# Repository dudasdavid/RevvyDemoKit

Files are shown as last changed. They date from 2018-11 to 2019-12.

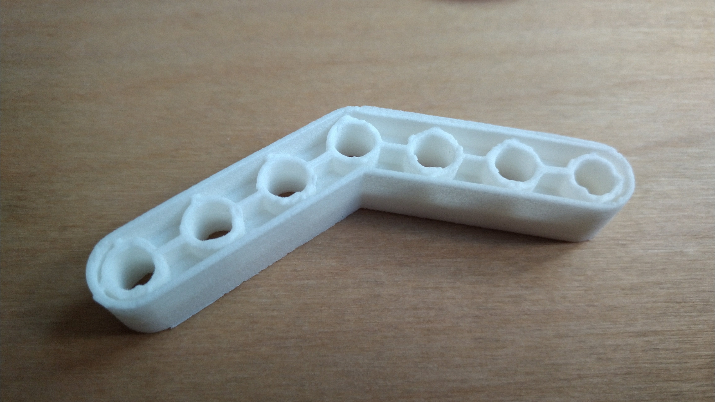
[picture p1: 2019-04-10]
Structural parts/QuotationSet2/Failure report/A135.jpg

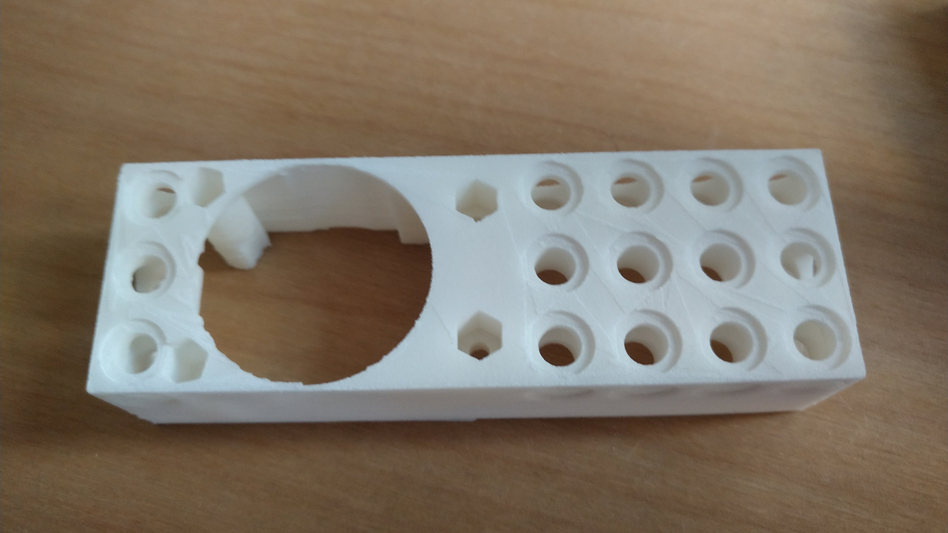
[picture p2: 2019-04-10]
Structural parts/QuotationSet2/Failure report/MOcA_1.jpg

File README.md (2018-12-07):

# RevvyDemoKit

Generated by STM32CubeMX 5.0.0 with STM32CubeF4 Firmware Package V1.22.0 / 02-November-2018

2018-11-03:
- 6x 20kHz PWM
- 6x 50Hz PWM
- WS2812 driver with DMA for 4 LEDs
- 6 ADC with DMA
- EXTI for 6 motor encoders using direction bit
- EXTI for 4 sensors
- GPIO inputs and outputs

2018-11-04:
- Cleanup of unused source files
- Cleanup of naming conventions in CubeMX project
- 4x ultrasonic distance sensors are working with 10us resolution based on TIM10
- 6x encoder signals are processed to distance [m], angle [deg] and velocity [m/s]
- Accelerometer and compass is working on I2C1 interface
- Roll and pitch angles are calculated from accelerometer
- Buzzer added TIM9_CH2

2018-11-14:
- Schematic is now uploaded
- WS2812 was unreliable with TIM+DMA, it might be a HW bug in ST's HW
- WS2812 is now driven on SPI5+DMA, pin moved to PB8 from PB7
- WS2812 library contains new functions to support SPI+DMA

2018-11-16:
- Final schematic added
- Gerber files added
- 3D model added

2018-11-17:
- Structural parts added

2018-11-19:
- WS2812 library cleanup, 3Mbit/s SPI is used, bit time is 1us

2018-11-24:
- Toolchain updated to STM32CubeMX 5.0.0 with STM32CubeF4 Firmware Package V1.22.0 / 02-November-2018
- Bluetooth tested
- Battery voltage measurement factor corrected

2018-12-07:
- Toolchain updated to STM32CubeMX 5.0.0 with STM32CubeF4 Firmware Package V1.23.0 / 23-November-2018
- First 4 WS2812 LEDs are showing the status of batteries and Bluetooth connection
- Communication protocol was updated to receive 5 bytes instead of 3
- PID controllers are added, 4 for velocity and 2 for angle

No patch is needed after code generation!

ToDo:
- Compass is not calibrated yet
- USB Host?

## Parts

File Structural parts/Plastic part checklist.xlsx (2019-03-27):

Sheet: Sum
Plastic Parts
Component / Cost Driver | RRF Part # | Color | In pool assem. | CAD file | STEP file | STL file | Volume [mm3] | Combined part | Comment | Remark/ Highlight
Straight Beams - S2x1 | S2x1 | White - P 1-1 C | OK |  |  |  | 897.51 | ok |  | According to spec; See CAD files….;
Straight Beams - S3x1 | S3x1 | White - P 1-1 C | OK |  |  |  | 1327.315 | ok
Straight Beams - S4x1 | S4x1 | White - P 1-1 C | OK |  |  |  | 1757.121 | ok
Straight Beams - S5x1 | S5x1 | White - P 1-1 C | OK |  |  |  | 2186.926 | ok
Straight Beams - S8x1 | S8x1 | White - P 1-1 C | OK |  |  |  | 3476.342 | ok
Straight Beams - S12x1 | S12x1 | White - P 1-1 C | OK |  |  |  | 5195.562 | ok
Straight Beams - S16x1 | S16x1 | White - P 1-1 C | OK |  |  |  | 6914.783 | ok
Straight Beams - S4x2 | S4x2 | White - P 1-1 C | OK |  |  |  | 3293.142 | ok
Straight Beams - S6x2 | S6x2 | White - P 1-1 C | OK |  |  |  | 4847.162 | ok
Straight Beams - S8x2 | S8x2 | White - P 1-1 C | OK |  |  |  | 6401.183 | ok
Straight Beams - S12x2 | S12x2 | White - P 1-1 C | OK |  |  |  | 9509.225 | ok
Straight Beams - S16x2 | S16x2 | White - P 1-1 C | OK |  |  |  | 12617.267 | ok
Straight Beams - S24x2 | S24x2 | White - P 1-1 C | OK |  |  |  | 18833.35 | ok
Straight Beams - S4x3 | S4x3 | White - P 1-1 C | OK |  |  |  | 4829.162 | ok
Straight Beams - S4x4 | S4x4 | White - P 1-1 C | OK |  |  |  | 6365.183 | ok
Straight Beams - S8x4 | S8x4 | White - P 1-1 C | OK |  |  |  | 12250.867 | ok
Angled Beams - A135 | A135 | White - P 1-1 C | OK |  |  |  | 3040.197 | ok
Angled Beams - A120 | A120 | White - P 1-1 C | OK |  |  |  | 3036.489 | ok
Angled Beams - A90L | A90L | White - P 1-1 C | OK |  |  |  | 2158.381 | ok
Angled Beams - A90T | A90T | White - P 1-1 C | OK |  |  |  | 2137.413 | ok
Curved Beams - CB4H | CB4H | Copper - 7579 C | OK |  |  |  | 2351.412 | ok
Curved Beams - CB6H | CB6H | Copper - 7579 C | OK |  |  |  | 3398.395 | ok
Round Beams - RB1 | RB1 | Silver - 649 C | OK |  |  |  | 829.393 | ok
Round Beams - RB2 | RB2 | Silver - 649 C | OK |  |  |  | 1271.18 | ok
Round Beams - RB3 | RB3 | Silver - 649 C | OK |  |  |  | 1712.966 | ok
Round Beams - RB4 | RB4 | Silver - 649 C | OK |  |  |  | 2154.753 | ok
Round Beams - RB8 | RB8 | Silver - 649 C | OK |  |  |  | 3921.898 | ok
Round Beams - RB12 | RB12 | Silver - 649 C | OK |  |  |  | 5689.044 | ok
Round Beams - RB16 | RB16 | Silver - 649 C | OK |  |  |  | 7456.19 | ok
Wedges - WE5x4 | WE5x4 | Gold - 7563 C | OK |  |  |  | 4241.774 | ok
Connector Triangle CT2x2 | CT2x2 | Blue - 285 C | OK |  |  |  | 2245.569 | ok
Connector Cubes - CC1x1 | CC1x1 | Blue - 285 C | OK |  |  |  | 1312.221 | ok
Connector Cubes - CC2x2 | CC2x2 | Blue - 285 C | OK |  |  |  | 3499.375 | ok
Connector Pins - CP1x1 | CP1x1 | Red - 185 C | OK |  |  |  | 387.607 | ok
Connector Pins - CP2x1 | CP2x1 | Copper - 7579 C | OK |  |  |  | 543.138 | ok
Connector Pins - CP2x2 | CP2x2 | Gold - 7563 C | OK |  |  |  | 698.668 | ok
Wheels - WHrM | WHrM | White - P 1-1 C | OK
Wheels - WHtM | WHtM | Black - Neutral Black C | OK
Gears - G20 | G20 | Blue - 285 C | OK |  |  |  | 1227.196 | ok
Gears - G40 | G40 | Blue - 285 C | OK |  |  |  | 4843.868 | ok
Gears - G60 | G60 | Blue - 285 C | OK |  |  |  | 6677.019 | ok
Elevators - EL8 | EL8 | Blue - 285 C | OK |  |  |  | 5425.347 | ok
Axels - AXp2c | AXp2c | Black - Neutral Black C | OK |  |  |  | 340.899 | ok
Axels - AXp3c | AXp3c | Black - Neutral Black C | OK |  |  |  | 480.15 | ok
Axels - AXp3s | AXp3s | Black - Neutral Black C | OK |  |  |  | 418.597 | ok
Axels - AXp6s | AXp6s | Black - Neutral Black C | OK |  |  |  | 838.155 | ok
Axels - AXp12s | AXp12s | Black - Neutral Black C | OK |  |  |  | 1677.269 | ok
Axels - AXp2p | AXp2p | Black - Neutral Black C | OK |  |  |  | 340.076 | ok
Axels - AXp4p | AXp4p | Black - Neutral Black C | OK |  |  |  | 636.353 | ok |  | My suggestion is to create
Axel Beams - AXb1 | AXb1 | Red - 185 C | OK |  |  |  | 1452.922 | ok
Axel Beams - AXb3 | AXb3 | Red - 185 C | OK |  |  |  | 2350.432 | ok
Motor Cases - MOcA_1 - No conn. Side | MOcA_1 | Red - 185 C | OK
Motor Cases - MOcA_2 - Conn. Side | MOcA_2 | Red - 185 C | OK
Motor Horns - MOhA_1 - Pin inside | MOhA_1 | Red - 185 C | OK
Motor Horns - MOhA_2 - No pin inside | MOhA_2 | Red - 185 C | OK
Brain Case - BRcA_1 Bottom | BRcA_1 | Black - Neutral Black C | OK |  |  |  |  |  |  | do we want a different finish?
Brain Case - BRcA_2 Top | BRcA_2 | Black - Neutral Black C | OK |  |  |  |  |  |  | do we want a different finish?
Brain Case - BRcA_3 Logo part | BRcA_3 | Mixed | OK |  |  |  |  |  |  | do we want a different finish?
Ultrasonic Sensor Case - UScA_1 Conn side | UScA_1 | Red - 185 C | OK
Ultrasonic Sensor Case - UScA_2 No conn side | UScA_2 | Red - 185 C | OK
Bumper Switch Case - BUcA_1 Conn side | BUcA_1 | White - P 1-1 C | OK
Bumper Switch Case - BUcA_2 No conn side | BUcA_2 | White - P 1-1 C | OK
Bumper Switch Case - BUcA_3 Button | BUcA_3 | Red - 185 C | OK
Rubber Bands - RBs | RBs | ?
Rubber Bands - RBm | RBm | ?
Caster Wheel Base - CWbA | CWbA | Blue - 285 C | OK
AA Battery Pack Case - BAcA_1 | BAcA_1 | Black - Neutral Black C | OK
AA Battery Pack Case - BAcA_2 | BAcA_2 | Black - Neutral Black C | OK
Parts not needed:
Washers - WashS | WashS | Any color |  |  |  |  |  |  | Not needed
Wedges - WE5x8 | WE5x8 | Gold - 7563 C |  |  |  |  | Not needed | xxx | Not needed
Connector Triangle CT3x3 | CT3x3 | Blue - 285 C |  |  |  |  | 3493.933 | ok | Not needed
Axels - AXp3p | AXp3p | Black - Neutral Black C |  |  |  |  | 497.102 | ok | Not needed
Straight Beams - S24x1 | S24x1 | White - P 1-1 C |  |  |  |  | 10353.225 | ok | Not needed
Angled Beams - A90P | A90P | White - P 1-1 C |  |  |  |  | 2588.186 | ok | Not needed

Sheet: Color Codes
Name | Red | Green | Blue
Black - Neutral Black C | 26 | 26 | 26
Blue - 285 C | 2 | 100 | 255
Copper - 7579 C | 198 | 83 | 35
Gold - 7563 C | 213 | 154 | 44
Red - 185 C | 230 | 3 | 18
Silver - 649 C | 236 | 236 | 236
White - P 1-1 C | 255 | 255 | 255

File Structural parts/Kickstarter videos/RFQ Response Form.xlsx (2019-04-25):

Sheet: RFQ Cost Drivers
Client: | Revolution Robotics Foundation (a 501c3 registered non-profit charity)
Product Name: | Educational Robotics Kit
Instructions: | Please complete the RFQ by entering data into each green shaded cell in this worksheet. Responses due by February 28th.
Robot Brain (1 per kit)
Component / Cost Driver | RRF Part # | Requirements | Additional Notes | CM Comments & Assumptions | Design Costs | One-Time Set-up Costs | Trial Run of 1,000 kits | 5,000 kit production run | 10,000 kit production run
RaspberryPi Zero W | PiZWA | Must be an official RaspberryPi Zero W | If CM cannot procure in sufficient volume, then Revolution Robotics will supply these to the CM.
16GB TF Card (Micro) | TF16gbA | Class 10 UHS U1 - to be selected by CM
TF Card Imaging | (not a part) | Customer will provide the software to be imaged onto the TF Card. No software to be developed by CM.
Brain LED PCB (including components) | BRled1 | See "Brain LED PCB" folder in OneDrive for specifications | Include full BoM cost here.
Brain LED Assembly | BRledA | See "Brain LED PCB" folder in OneDrive for specifications
Carrier Board Component #1 | JHY813270 | Battery, Li-Ion, 3.7V, 2000mAh, 8.1x32x70.5, 0/+45 | 1 per kit
Carrier Board Component #2 | CC0402KRX5R6BB475 | Capacitor, 4.7u, 10V, X5R, 10%, 0402 | 2 per kit |  | please provide all prices on a "per kit" basis
Carrier Board Component #3 | CL31A106KAHNNNE | Capacitor, 10u, 25V, X5R, 10%, -55/+85, 1206 | 29 per kit
Carrier Board Component #4 | CC0402KRX7R7BB104 | Capacitor, 100n, 16V, X7R, 10%, 0402 | 43 per kit
Carrier Board Component #5 | CL21A226KPCLRNC, CC0805MKX5R7BB226 | Capacitor, 22u, 10V, X5R, 10%, -55/+85, 0805, Capacitor, 22u, 16V, X5R, 20%, -55/+85, 0805 | 8 per kit
Carrier Board Component #6 | CC0402KRX7R7BB103 | Capacitor, 10n, 16V, X7R, 10%, 0402 | 12 per kit
Carrier Board Component #7 | GCM155R71H222KA37D | Capacitor, 2.2n, 50V, X7R, 10%, -55/+125, 0402 | 3 per kit
Carrier Board Component #8 | CC0402KRX5R7BB105 | Capacitor, 1u, 16V, X5R, 10%, 0402 | 9 per kit
Carrier Board Component #9 | CC0603KRX5R7BB475 | Capacitor, 4.7u, 16V, X5R, 10%, -55/+85, 0603 | 2 per kit
Carrier Board Component #10 | CC0402KRX7R9BB102 | Capacitor, 1n, 50V, X7R, 10%, 0402 | 1 per kit
Carrier Board Component #11 | C0402C224K9PACTU | Capacitor, 220nF, 6.3V, X5R, 10%, -55/+85, 0402 | 1 per kit
Carrier Board Component #12 | CC0402KRX7R7BB333 | Capacitor, 33n, 16V, X7R, 10%, 0402 | 1 per kit
Carrier Board Component #13 | GRPB051VWVN-RC | Conn, Header, Vertical, 5POS, P-1.27, -40/+105, TH | 1 per kit
Carrier Board Component #14 | RJHSE538103 | Conn, RJ-45, Right Angle, 3pos, Shielded, -55/+85, TH | 2 per kit
Carrier Board Component #15 | PJ-037A | Conn, DC Jack, 2pos, 2.1m - 5.5mm, TH | 1 per kit
Carrier Board Component #16 | PPTC202LJBN-RC | Conn, Header,RA, Female, 20x2POS, P-2.54mm, -40/+105, TH | 1 per kit
Carrier Board Component #17 | RJHSE538104 | Conn, RJ-45, Right Angle, 4pos, Shielded, -55/+85, TH | 1 per kit
Carrier Board Component #18 | BM05B-SRSS-TB(LF)(SN) | Conn, Header, Vertical, Male pin 5POS, P-1mm, -25/+85, SMD | 1 per kit
Carrier Board Component #19 | CPDQ5V0-HF | Diode, TVS, 5VWM, 18.6VC, -40/+125, SOD-923F | 24 per kit
Carrier Board Component #20 | LXES15AAA1-133 | Diode, TVS, 15V, -40/+85, 0402 | 13 per kit
Carrier Board Component #21 | PDS1040Q-13 | Diode, Schottky, AEC-Q101, 40V, 10A, -65/+150, POWERDI5 | 1 per kit
Carrier Board Component #22 | TPD6E001RSER | Diode, TVS, 6-ch, 5VWM, 11VC, -55/+150, UFQFN-10 | 3 per kit
Carrier Board Component #23 | CPDQ3V3-HF | Diode, TVS, 3.3VWM, 18.6VC, -40/+125, SOD-923F | 20 per kit
Carrier Board Component #24 | BAT54GWJ | Diode, Schottky, 30V, 200mA, -55/+150, SOD-123 | 8 per kit
Carrier Board Component #25 | BLM18AG121SN1D | Ferrite Bead, 0.5A, 120 Ohm/100MHz, -55/+125, 0603 | 2 per kit
Carrier Board Component #26 | BKP1005EM600-T | Ferrite Bead, 1.7A, 60 Ohm/100MHz, -55/+85, 0402 | 1 per kit
Carrier Board Component #27 | BKP1005EM221-T | Ferrite Bead, 1A, 220Ohm/100MHz, -55/+85, SMD, 0402 | 4 per kit
Carrier Board Component #28 | BKP1005HS221-T | Ferrite Bead, 0.8A, 220 Ohm/100MHz, -55/+85, 0402 | 4 per kit
Carrier Board Component #29 | 0ZCK0075FF2E | Fuse, PTC, Resettable, 0.75A, 6V, 0805 | 20 per kit
Carrier Board Component #30 | BRL3225T100K | Inductor, 10uH, 0.7A, 10%, 420mOhm, Wirewound, -40/+105, 3.2x2.5x1.7 | 1 per kit
Carrier Board Component #31 | IHLP2020BZER1R0M11 | Inductor, 1uH, 7A, 20%, 18.1mOhm, Shielded, -55/+125, 5.18x5.18x2 | 2 per kit
Carrier Board Component #32 | Raspberry Pi Zero W | 1Ghz CPU, 512MB RAM, Bluetooth 4.1, 802.11 b/g/n wireless LAN | 1 per kit
Carrier Board Component #33 | PRPC020DAAN-RC | Conn, Header, Male, 20x2POS, P-2.54mm, -40/+105, TH | 1 per kit
Carrier Board Component #34 | SHR-05V-S-B | Conn, Female Socket, Housing, 5 pin, 1 mm | 1 per kit
Carrier Board Component #35 | SSH-003T-P0.2-H | Crimp Receptacle Terminal, Female, 28-32AWG | 6 per kit
Carrier Board Component #36 | NX7002AK,215 | MOSFET, N-CH, 60V, 190mA, -55/+150, TO-236AB | 16 per kit
Carrier Board Component #37 | DMP3099L-13 | MOSFET, P-CH, 30V, 3.8A, -55/+150, SOT-23 | 1 per kit
Carrier Board Component #38 | SSM3J35AMFV,L3F | MOSFET, P-CH, 20V, 250mA, -55/+150, SOT-723 | 1 per kit
Carrier Board Component #39 | RC0402FR-0710KL | Resistor, 10K, 0.063W, 1%, -55/+155, 0402 | 5 per kit
Carrier Board Component #40 | RC0402FR-07100KL, [NoValue] | Resistor, 100K, 0.063W, 1%, -55/+155, 0402, Resistor, 100K, 0.0625W, 1%, 0402 | 10 per kit
Carrier Board Component #41 | RC0402FR-0747KL | Resistor, 47K, 0.063W, 1%, -55/+155, 0402 | 44 per kit
Carrier Board Component #42 | RC0402FR-07680RL | Resistor, 680, 0.0625W, 1%, 0402 | 20 per kit
Carrier Board Component #43 | RC0402FR-07100RL | Resistor, 100, 0.063W, 1%, -55/+155, 0402 | 29 per kit
Carrier Board Component #44 | RC0402FR-071KL | Resistor, 1K, 0.063W, 1%, -55/+155, 0402 | 4 per kit
Carrier Board Component #45 | RC0402FR-0730KL | Resistor, 30K, 0.0625W, 1%, 0402 | 1 per kit
Carrier Board Component #46 |  | Resistor, 2K, 0.0625W, 1%, 0402 | 1 per kit
Carrier Board Component #47 | RC0402FR-071ML | Resistor, 1M, 0.0625W, 1%, 0402 | 2 per kit
Carrier Board Component #48 | RC0402FR-07910KL | Resistor, 910K, 0.0625W, 1%, 0402 | 1 per kit
Carrier Board Component #49 | RC0402FR-07240KL | Resistor, 240K, 0.0625W, 1%, 0402 | 1 per kit
Carrier Board Component #50 | RC0402FR-07200KL | Resistor, 200K, 0.0625W, 1%, 0402 | 1 per kit
Carrier Board Component #51 | RC0402FR-07820KL | Resistor, 820K, 0.0625W, 1%, 0402 | 1 per kit
Carrier Board Component #52 | RC0402FR-07205KL | Resistor, 205kOhms, 1%, 0.063W, -55/+155, 0402 | 1 per kit
Carrier Board Component #53 | RC0402FR-0720KL | Resistor, 20K, 0.0625W, 1%, 0402 | 2 per kit
Carrier Board Component #54 | RC0402FR-07270RL | Resistor, 270, 0.0625W, 1%, 0402 | 1 per kit
Carrier Board Component #55 | RC0402FR-07150RL | Resistor, 150, 0.0625W, 1%, 0402 | 1 per kit
Carrier Board Component #56 | RC0402FR-074K7L | Resistor, 4.7K, 0.063W, 1%, -55/+155, 0402 | 16 per kit
Carrier Board Component #57 | RC0402FR-07150KL | Resistor, 150K, 0.0625W, 1%, 0402 | 4 per kit
Carrier Board Component #58 | 500SDP1S1M7QEA | Conn, Slide Switch, Vertical, DPDT, Shielded, 3.81mm, -20/+85, TH | 1 per kit
Carrier Board Component #59 | ATSAMD51P19A-AUT | IC,MCU,32-bit,ARM Cortex M4,Flash 512K,1.8-3.6V,-40/+85, TQFP-128 | 1 per kit. Must be an official Microchip MCU model ATSAMD51P19A-AU; If CM cannot procure in sufficient volume, then Revolution Robotics will supply these to the CM. | Please indicate if the MCU will be procured in Reels or in Trays
Carrier Board Component #60 | ACS711KEXLT-15AB-T | IC, Hall effect current sensor, 15.5A, 3 - 5.5V, 90mV/A, -40/+125, 12-QFN | 1 per kit |  |  |  |  |  |  | 1 per kit
Carrier Board Component #61 | LDL212PU50R | IC, VolReg, LDO, 18V/5V, 1.2A, -40/+125, DFN-6 | 6 per kit |  |  |  |  |  |  | 6 per kit
Carrier Board Component #62 | NTS0104GU12,115 | IC,4-Ch Level Translator Bidir, 2.3V - 5.5V, 20Mbps, -55/+125, 12-XQFN | 4 per kit |  |  |  |  |  |  | 4 per kit
Carrier Board Component #63 | AP7362-33SP-13 | IC, VolReg, LDO, 5.5V/3.3V, 1.5A, -40/+85, SO-8 | 1 per kit |  |  |  |  |  |  | 1 per kit
Carrier Board Component #64 | TB6612FNG,C,8,EL | IC, 2-ch Half-bridge, 2.7V - 5.5V / 2.5V - 13.5V, -20/+85, SSOP-24 | 3 per kit |  |  |  |  |  |  | 3 per kit
Carrier Board Component #65 | BQ24092DGQR | IC, Li-Po CHRG, 1A, 4.2V, 0/+125, MSOP-10 | 1 per kit |  |  |  |  |  |  | 1 per kit
Carrier Board Component #66 | MIC2876-AYMT-TR | IC, Boost Controller, 2.5V-5.5V/Adj, 3.8A, -40/+85, TDFN-8 | 2 per kit |  |  |  |  |  |  | 2 per kit
Carrier Board Component #67 | LM393DR2GH | IC, Linear Comparator, 2-ch,2V-30V, +-1V - +-18V, 0/+70, SOIC-8 | 1 per kit |  |  |  |  |  |  | 1 per kit
Carrier Board Component #68 | IS31AP4991-GRLS2-TR | IC, Audio amplifier, Mono, 2.7V - 5.5V, -40/+85, SOIC-8 | 1 per kit |  |  |  |  |  |  | 1 per kit
Brain PCB Board | BRpcb1 | "Carrier Board"
Brain PCBA Assembly | BRpcbA | Please see "Brain PCBA" folder in OneDrive for specifications | Customer to provide firmware for CM to flash onto MCU. Pricing must include SMT and Testing; The CM's chosen 4-port RJ45 jack on the front of the brain must be no wider than 63.1mm.
Brain Test Stand | (not a part) | Please recommend test tools and proceedures along with their costs.
Battery - 2000mAh LiPo | BAbrA | Maximum space available for this LiPo battery is 85mm x 39mm x 8mm | The battery should be at least 50% charged when shipped.
Brain Case (Plastic) | BRcA | See corresponding file in OneDrive | Please indicate any labelling requirements and labelling method (e.g., polycarbonate label floated into debossed rectangle)
External Serialization | (part of label) | CM must extract the unique CPU Serial Number from each RaspberryPi Zero W and include that number on the "label" on the outside of the Brain Case.
Final Assembly | BRbeta | Fasteners TBD based on CM recommendation (e.g., snap-fit, nuts, bolts, screws, glue, etcetera); Must include a final test for successful operation.
Packaging | (TBD if required) | Includes protective packaging (e.g., in a polybag placed into a polytray in E Flute box)
Motors (5 per kit)
Component / Cost Driver | RRF Part # | Requirements | Additional Notes | CM Comments & Assumptions | Design Costs | One-Time Set-up Cost | Trial Run of 1,000 kits (5,000 motors) | 5,000 kit production run (25k motors) | 10,000 kit production run (50k motors)
6v DC Motor | MOdc6VA | See "Motor Specifications" tab & OneDrive files |  |  |  |  | Please remember to price in terms of kits which include 5 motors each
Gearbox | MOgbA | See "Motor Specifications" tab & OneDrive files
Encoder | MOenA | See "Motor Specifications" tab & OneDrive files
RJ45 female | RJ45x1A | See "Motor Specifications" tab & OneDrive files | Pinout of RJ45 to be provided by Customer; no LED's required on jack
Motor PCB Design | (design only) | See "Motor Specifications" tab & OneDrive files | Connects the encoder, RJ45 and motor contacts; designed by CM
Motor PCB Assembly | MOpcbA | See "Motor Specifications" tab & OneDrive files | Physically attaching motor contacts, encoder & RJ45 jack
Motor Horns (Plastic) | MOcA | See "Motor Specifications" tab & OneDrive files | Also see "Plastic Parts BoM" tab
Motor Case (Plastic) | MOhA | See "Motor Specifications" tab & OneDrive files | Also see "Plastic Parts BoM" tab
Final Assembly | MObeta | Fasteners TBD based on CM recommendation (e.g., snap-fit, nuts, bolts, screws, glue, etcetera); Final Assembly must include a final performance test
Packaging | (TBD if required) | Includes protective packaging (e.g., in a polybag placed into a polytray in E Flute box)
Bump Switch (1 per kit)
Component / Cost Driver | RRF Part # | Requirements | Additional Notes | CM Comments & Assumptions | Design Costs | One-Time Set-up Costs | Trial Run of 1,000 kits | 5,000 kit production run | 10,000 kit production run
Bump Switch (electronic component) | BUcomA | 5,000 click reliability
Spring for Bumper | BUsprA | 3mm travel, 1N force at the end | auxillary spring...
RJ45 female | RJ45x1A |  | Pinout by customer, no LED's required
Bump Switch PCB Design | (design only) | See "Bumper Switch" in OneDrive | super simple to connect the Bump Switch electronic component to the RJ45 jack
Bump Switch PCB Assembly | BUpcbA | See "Bumper Switch" in OneDrive | Physically attaching Bump Switch electronic component and RJ45 jack to PCB
Bump Switch Case (Plastic) | BUcA | See "Bumper Switch" in OneDrive; The plastic casing must provide a mechanical stop to protect the Bump Switch electronic component (part "BUcomA") and the PCB it attaches to from receiving too much force (e.g., exceeding the switch's nominal value) | Also see "Plastic Parts BoM" tab; CM is encouraged to reduce the size of this overall case in their design
Final Assembly | BUbeta | Fasteners TBD based on CM recommendation (e.g., snap-fit, nuts, bolts, screws, glue, etcetera); Final Assembly must include a final performance test
Packaging | (TBD if required) | Includes protective packaging (e.g., heatsealed mylar bag)
Ultrasonic Range Sensor (1 per kit)
Component / Cost Driver | RRF Part # | Requirements | Additional Notes | CM Comments & Assumptions | Design Costs | One-Time Set-up Costs | Trial Run of 1,000 kits | 5,000 kit production run | 10,000 kit production run
Ultrasonic Range Sensor (TX/RX electronic component) | UScomA | HC-SR04 sensor or equivalent | A smaller sized board is preferred.
RJ45 female | RJ45x1A | Pinout to be provided by Customer; no LED's required
Ultrasonic Range Sensor PCB Design | (design only) | CM to design to simply connect sensor to the RJ45 jack
Ultrasonic Range Sensor PCB Assembly | USpcbA | Physically attaching the sensor and RJ45 jack to PCB
Ultrasonic Range Sensor Case (Plastic) | UScA | See "Ultrasonic Sensor" in OneDrive | Also see "Plastic Parts BoM" tab; CM is encouraged to reduce the size of this overall case in their design
Final Assembly | USbeta | Fasteners TBD based on CM recommendation (e.g., snap-fit, nuts, bolts, screws, glue, etcetera); Final Assembly must include a final performance test
Packaging | (TBD if required) | Includes protective packaging (e.g., heatsealed mylar bag)
AA Battery Pack (1 per kit)
Component / Cost Driver | RRF Part # | Requirements | Additional Notes | CM Comments & Assumptions | Design Costs | One-Time Set-up Costs | Trial Run of 1,000 kits | 5,000 kit production run | 10,000 kit production run
6x Rechargeable AA Batteries | BA6xAA | 6 batteries per kit. Ni-MH 1.2V min.2000mAh | Must be packaged for storage and shipping as part of the overall kit; Should be at least 50% charged when shipped
Battery Holder Tray (holds 6x AA) | BAtrayA | Holds 6x AA batteries for easy swap of individual AA batteries by the end user without necessarily having to remove the entire battery pack casing from the robot | CM to recommend battery tray with fit & locking mechanism along with
DC plug (male end with wire) | BAplugA | Must be compatable with the DC female on the Brain (5.5mm outer diameter, 2.1mm inner diameter is preferred); Wire length of ~16cm is desired.
Battery Pack Case (Plastic) | BAcA | See "Plastic Parts BoM" tab; CM is highly to modify the design for ease of use, cost & manufacturability
Final Assembly | BAbeta | Fasteners TBD based on CM recommendation (e.g., snap-fit, nuts, bolts, screws, glue, etcetera); Final testing NOT required
Packaging | (TBD if required) | CM to recommend if protective packaging is required
Caster Wheel (1 per kit)
Component / Cost Driver | RRF Part # | Requirements | Additional Notes | CM Comments & Assumptions | Design Costs | One-Time Set-up Costs | Trial Run of 1,000 kits | 5,000 kit production run | 10,000 kit production run
Caster Wheel | CWpA | See "Caster Wheel" files in OneDrive | Can be plastic, metal or some combination to provide lowest cost solution.
Caster Wheel Base (Plastic) | CWbA | See "Plastic Parts BoM" tab; CM is highly to modify the design for cost & manufacturability | Should be similar to the S4x3 or S4x4 Plastic Part
Final Assembly | CWbeta | Fasteners TBD based on CM recommendation (e.g., snap-fit, nuts, bolts, screws, glue, etcetera); Final testing NOT required, but ball must roll smoothly when 2kg of force is applied from above the overall part
Plastic Parts | For every Plastic Part (including Cases), CM is encouraged to propose design modifications to improve cost, manufacturability and / or function
Component / Cost Driver | RRF Part # | Requirements | Additional Notes | CM Comments & Assumptions | Design Costs | One-Time Set-up Costs | Trial Run of 1,000 kits | 5,000 kit production run | 10,000 kit production run
Straight Beams - S2x1 | S2x1 | Please also refer to files with matching names in OneDrive
Straight Beams - S3x1 | S3x1
Straight Beams - S4x1 | S4x1
Straight Beams - S5x1 | S5x1
Straight Beams - S8x1 | S8x1
Straight Beams - S12x1 | S12x1
Straight Beams - S16x1 | S16x1 | Must be able to balance 4kg on each end with a fulcrum under the center of the length of the beam. It can bend, but cannot break.
Straight Beams - S4x2 | S4x2
Straight Beams - S6x2 | S6x2
Straight Beams - S8x2 | S8x2
Straight Beams - S12x2 | S12x2
Straight Beams - S16x2 | S16x2
Straight Beams - S24x2 | S24x2 | Must be able to balance 4kg on each end with a fulcrum under the center of the length of the beam. It can bend, but cannot break.
Straight Beams - S4x3 | S4x3
Straight Beams - S4x4 | S4x4
Straight Beams - S8x4 | S8x4
Angled Beams - A135 | A135
Angled Beams - A120 | A120
Angled Beams - A90L | A90L
Angled Beams - A90T | A90T
Curved Beams - CB4H | CB4H
Curved Beams - CB6H | CB6H
Round Beams - RB1 | RB1
Round Beams - RB2 | RB2
Round Beams - RB3 | RB3
Round Beams - RB4 | RB4
Round Beams - RB8 | RB8
Round Beams - RB12 | RB12
Round Beams - RB16 | RB16 | Must be able to balance 4kg on each end with a fulcrum under the center of the length of the beam. It can bend, but cannot break.
Wedges - WE5x4 | WE5x4
Connector Triangle - CT2x2 | CT2x2
Connector Cubes - CC1x1 | CC1x1
Connector Cubes - CC2x2 | CC2x2
Connector Pins - CP1x1 | CP1x1 | Should snap into the 5mm holes on beams and be able to rotate freely with minimal friction. The user experience should be similar to using a Lego Technic pin # 32556 to snap into and rotate within various connection holes along various Lego Technic beams.
Connector Pins - CP2x1 | CP2x1 | Should snap into the 5mm holes on beams and be able to rotate freely with minimal friction. The user experience should be similar to using a Lego Technic pin # 32556 to snap into and rotate within various connection holes along various Lego Technic beams.
Connector Pins - CP2x2 | CP2x2 | Should snap into the 5mm holes on beams and be able to rotate freely with minimal friction. The user experience should be similar to using a Lego Technic pin # 32556 to snap into and rotate within various connection holes along various Lego Technic beams.
Wheels - WHrM | WHrM
Wheels - WHtM | WHtM
Gears - G20 | G20
Gears - G40 | G40
Gears - G60 | G60
Elevators - EL8 | EL8
Axels - AXp2c | AXp2c
Axels - AXp3c | AXp3c
Axels - AXp3s | AXp3s
Axels - AXp6s | AXp6s
Axels - AXp12s | AXp12s
Axels - AXp2p | AXp2p
Axels - AXp4p | AXp4p
Axel Beams - AXb1 | AXb1
Axel Beams - AXb3 | AXb3
Motor Cases - MOcA | MOcA | (see above in Motors section) |  | (please price above in Motors section)
Motor Horns - MOhA | MOhA | (see above in Motors section) |  | (please price above in Motors section)
Brain Case - BRcA | BRcA | (see above in Brain section) |  | (please price above in Brain section)
Ultrasonic Sensor Case - UScA | UScA | (see above in Ultrasonic Sensor section) |  | (please price above in Ultrasonic Sensor section)
Bump Switch Case - BUcA | BUcA | (see above in Bump Switch section) |  | (please price above in Bump Switch section)
AA Battery Pack Case - BAcA | BAcA | (see above in AA Battery Pack section) |  | (please price above in AA Battery Pack section)
Caster Wheel Base - CWpA | CWpA | (see above in the Caster Wheel section) |  | (please price above in Caster Wheel section)
Other Standard Parts in Kit
Component / Cost Driver | RRF Part # | Requirements | Additional Notes | CM Comments & Assumptions | Design Costs | One-Time Set-up Costs | Trial Run of 1,000 kits | 5,000 kit production run | 10,000 kit production run
USB-A to micro-USB cable | USBcabA | Black. Between 50cm to 150cm in length. | 1 per kit. Used to recharge the LiPo battery housed in the Brain. Does NOT include a 'wall wart' or 'Edison plug' - it is just a cable.
RJ45 8pin network cable - Short | RJcabSA | ~8cm long. White. Flat ribbon cable with RJ45 jacks (8pin) on both ends. | 6 per kit. |  |  |  | (price per robot kit, not per cable)
RJ45 8pin network cable - Medium | RJcabMA | ~16cm long. White. Flat ribbon cable with RJ45 jacks (8pin) on both ends. | 4 per kit. |  |  |  | (price per robot kit, not per cable)
RJ45 8pin network cable - Long | RJcabLA | ~32cm long. White. Flat ribbon cable with RJ45 jacks (8pin) on both ends. | 2 per kit. |  |  |  | (price per robot kit, not per cable)
Rubber Bands (20+ per kit) | RB5A | Black, Red or Blue in color. Approximate diameter of 5cm (+ or - 1cm). Width of at least 2mm and not more than 5mm. | At least 20 per kit. Can be up to 50 per kit if it simplifies ordering and handling. |  |  |  | (price per robot kit, not per rubber band)
Ping Pong Balls (5+ per kit) | PPbA | Colors may vary. Should be at least 2 different colors, but every ball could be a different color. | At least 5 per kit. Can be up to 10 per kit if it simplifies ordering and handling. |  |  |  | (price per robot kit, not per ping pong ball)
Challenge Cones (4 per kit) | CCpA | Colors may vary. Should be at least 2 different colors, but every cone could be a different color. Diameter of hole on top should not be less than 41mm and not more than 65mm. Similar in size and shape to: https://www.alibaba.com/product-detail/Outdoor-soccer-and-football-plastic-marker_60690963849.html | At least 4 per kit. Can be up to 10 per kit if it simplifies ordering and handling. |  |  |  | (price per robot kit, not per cone)
USB powered 6x AA battery recharger with status LED | BAchgA | Power cable must be at least 10cm long with a USB male connector at one end. | 1 per kit. Used to recharge the AA batteries from the Battery Pack which powers the motors. Does NOT include a 'wall wart' or 'Edison plug' - it has just a USB-A end to the cable.
Kit Packing & Carton
Component / Cost Driver | RRF Part # | Requirements | Additional Notes | CM Comments & Assumptions | Design Costs | One-Time Set-up Costs | Trial Run of 1,000 kits | 5,000 kit production run | 10,000 kit production run
Blister tray(s) for expensive parts | (TBD) | Should fit snuggly into the External Carton (below) with depressions for Brain, 5 motors, sensors and potentially some other expensive and / or shock sensitive parts
Rest of parts bagged & put in loosly | (TBD) | All parts should be bagged. All bagged parts not in the Blister Tray(s) can have their bags put loosely into the External Carton (below)
Quick start guide | QSpA | 60# cover stock paper. A4 size. 4 color, 1-sided printing
Part List and Playing Field Poster | PFpA | 60# cover stock paper. The size of ~8 sheets of A4 paper (~60cm wide by ~84cm tall). Black ink + 2 PMS colors on one side, over Black (on the other side)
External Carton | KITbA | Roughly 30cm x 24cm x 16cm is our targeted size, but recommendations from CM are welcome. 4 color, 1-sided printing for the External Carton (e.g., 4-color giftbox)
Shrinkwrap of External Carton | (TBD)
Master Carton | MCbA | 5 robot kits (e.g., External Cartons) per Master Carton is preferred, but not required. Please optimize to pass drop testing & for loading onto pallets.
Regulatory / Certifications | CM needs to secure any certifications ensure kit meets any labeling requirements.
Governing Body | RRF Part # | Requirements | Additional Notes | CM Comments & Assumptions | Design Costs | One-Time Set-up Costs | Trial Run of 1,000 kits | 5,000 kit production run | 10,000 kit production run
FCC | - | CM to secure necessary certification.
RoHS | - | CM to secure necessary certification.
Prop65 | - | CM to secure necessary certification.
ASTM | - | CM to secure necessary certification.
CPSIA | - | CM to secure necessary certification.
CCC Phthalates | - | CM to secure necessary certification.
CE (Europe) | - | CM to secure necessary certification.
Bluetooth communication | - | CM to secure necessary certification.
Drop/shock test | - | CM to secure necessary certification. | IEC 60068-2-6 and IEC 60068-2-27
Other compliance requirements? (e.g., IC?) | - | Identify additional compliance or certification requirements not listed above.
Cost Summary | Design Costs | One-Time Set-up Costs | Trial Run of 1,000 kits | 5,000 kit production run | 10,000 kit production run
Total Cost (FOB to Yantian or Hong Kong)
Please indicate preferred FOB port:
Please indicate desired payment terms:
Please submit a draft MSA contract: | (please attach to RFQ response)
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

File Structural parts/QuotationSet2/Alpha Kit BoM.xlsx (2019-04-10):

Overall qty | Qty per alpha kit | RRF Part # | 20190329 shipment memos | Pack 1 bad | Pack 2 bad | Pack 3 bad | szum bad | % bad | Claim | Part Type | Status | Comment | Length (mm) | Width (mm) | Height (mm) | Volume (mm^3)
32 | 4 | S2x1 | ok | 0 | 0 | 0 | 0 | 0 | 0 | Straight Beams | OK | No change | 20 | 10 | 10 | 897.51
32 | 4 | S3x1 | ok | 0 | 0 | 0 | 0 | 0 | 0 | Straight Beams | OK | No change | 30 | 10 | 10 | 1327.315
32 | 4 | S4x1 | ok | 2 | 2 | 2 | 6 | 50 | 16 | Straight Beams | OK | No change | 40 | 10 | 10 | 1757.121
32 | 4 | S5x1 | ok | 0 | 0 | 0 | 0 | 0 | 0 | Straight Beams | OK | No change | 50 | 10 | 10 | 2186.926
32 | 4 | S8x1 | ok | 0 | 0 | 1 | 1 | 8.333333333 | 2.666666667 | Straight Beams | OK | No change | 80 | 10 | 10 | 3476.342
32 | 4 | S12x1 | ok | 2 | 3 | 2 | 7 | 58.33333333 | 18.66666667 | Straight Beams | OK | No change | 120 | 10 | 10 | 5195.562
32 | 4 | S16x1 | ok | 0 | 0 | 0 | 0 | 0 | 0 | Straight Beams | OK | No change | 160 | 10 | 10 | 6914.783
32 | 4 | S4x2 | ok | 3 | 0 | 0 | 3 | 25 | 8 | Straight Beams | OK | No change | 40 | 20 | 10 | 3293.142
32 | 4 | S6x2 | ok | 0 | 0 | 0 | 0 | 0 | 0 | Straight Beams | OK | No change | 60 | 20 | 10 | 4847.162
32 | 4 | S8x2 | ok | 0 | 0 | 0 | 0 | 0 | 0 | Straight Beams | OK | No change | 80 | 20 | 10 | 6401.183
32 | 4 | S12x2 | ok | 0 | 0 | 0 | 0 | 0 | 0 | Straight Beams | OK | No change | 120 | 20 | 10 | 9509.225
32 | 4 | S16x2 | ok | 0 | 0 | 0 | 0 | 0 | 0 | Straight Beams | OK | No change | 160 | 20 | 10 | 12617.267
32 | 4 | S24x2 | ok | 0 | 0 | 2 | 2 | 16.66666667 | 5.333333333 | Straight Beams | OK | No change | 240 | 20 | 10 | 18833.35
32 | 4 | S4x3 | ok | 0 | 0 | 1 | 1 | 8.333333333 | 2.666666667 | Straight Beams | OK | No change | 40 | 30 | 10 | 4829.162
48 | 6 | S4x4 | ok | 6 | 2 | 3 | 11 | 61.11111111 | 29.33333333 | Straight Beams | OK | No change | 40 | 40 | 10 | 6365.183
32 | 4 | S8x4 | ok | 1 | 3 | 0 | 4 | 33.33333333 | 10.66666667 | Straight Beams | OK | No change | 80 | 40 | 10 | 12250.867
32 | 4 | A135 | ok | 4 | 4 | 4 | 12 | 100 | 32 | Angled Beams | OK | No change | 40 | 40 | 10 | 3040.197
32 | 4 | A120 | ok | 0 | 0 | 0 | 0 | 0 | 0 | Angled Beams | OK | No change | 40 | 40 | 10 | 3036.489
96 | 12 | A90L | ok | 9 | 4 | 6 | 19 | 52.77777778 | 50.66666667 | Angled Beams | OK | No change | 30 | 30 | 10 | 2158.381
64 | 8 | A90T | ok | 8 | 8 | 8 | 24 | 100 | 64 | Angled Beams | OK | No change | 30 | 30 | 10 | 2137.413
32 | 4 | CB4H | ok | 3 | 3 | 3 | 9 | 75 | 24 | Curved Beams | OK | No change | 40+ | 10 | 10 | 2351.412
32 | 4 | CB6H | ok | 0 | 0 | 0 | 0 | 0 | 0 | Curved Beams | OK | No change | 60+ | 10 | 10 | 3398.395
32 | 4 | RB1 | ok | 0 | 0 | 0 | 0 | 0 | 0 | Round Beams | OK | pin, lightening thickening | 10+ | 5 | 5 | 829.393
32 | 4 | RB2 | ok | 0 | 0 | 0 | 0 | 0 | 0 | Round Beams | OK | pin, lightening thickening | 20+ | 5 | 5 | 1271.18
32 | 4 | RB3 | ok | 0 | 0 | 0 | 0 | 0 | 0 | Round Beams | OK | pin, lightening thickening | 30+ | 5 | 5 | 1712.966
32 | 4 | RB4 | ok | 0 | 0 | 0 | 0 | 0 | 0 | Round Beams | OK | pin, lightening thickening | 40+ | 5 | 5 | 2154.753
32 | 4 | RB8 | ok | 0 | 0 | 0 | 0 | 0 | 0 | Round Beams | OK | pin, lightening thickening | 80+ | 5 | 5 | 3921.898
32 | 4 | RB12 | ok | 0 | 0 | 0 | 0 | 0 | 0 | Round Beams | OK | pin, lightening thickening | 120+ | 5 | 5 | 5689.044
32 | 4 | RB16 | ok | 0 | 0 | 0 | 0 | 0 | 0 | Round Beams | OK | pin, lightening thickening | 160+ | 5 | 5 | 7456.19
32 | 4 | WE5x4 | ok | 0 | 0 | 0 | 0 | 0 | 0 | Wedges | OK | No change | 50 | 40 | 10 | 4241.774
96 | 12 | CT2x2 | ok | 1 | 1 | 4 | 6 | 16.66666667 | 16 | Connector Triangle | OK | pin change | 20+ | 20+ | 10 | 2245.569
32 | 4 | CC1x1 | ok | 2 | 4 | 4 | 10 | 83.33333333 | 26.66666667 | Connector Cubes | OK | pin change | 10+ | 10+ | 10 | 1312.221
128 | 16 | CC2x2 | ok | 7 | 11 | 9 | 27 | 56.25 | 72 | Connector Cubes | OK | pin change | 20+ | 20+ | 10 | 3499.375
600 | 75 | CP1x1 | ok | 0 | 0 | 0 | 0 | 0 | 0 | Connector Pins | OK | pin change | 20 | 5 | 5 | 387.607
200 | 25 | CP2x1 | ok | 0 | 0 | 0 | 0 | 0 | 0 | Connector Pins | OK | pin change | 30 | 5 | 5 | 543.138
80 | 10 | CP2x2 | ok | 0 | 0 | 0 | 0 | 0 | 0 | Connector Pins | OK | pin change | 40 | 5 | 5 | 698.668
32 | 4 | WHrM | ok | 0 | 0 | 0 | 0 | 0 | 0 | Wheels | OK | No change | 40 | 40 | 18
32 | 4 | G20 | ok | 0 | 0 | 0 | 0 | 0 | 0 | Gears | OK | No change | 20+ | 20+ | 8 | 1227.196
32 | 4 | G40 | ok | 3 | 4 | 3 | 10 | 83.33333333 | 26.66666667 | Gears | OK | No change | 40+ | 40+ | 8 | 4843.868
32 | 4 | G60 | ok | 2 | 4 | 4 | 10 | 83.33333333 | 26.66666667 | Gears | OK | No change | 60+ | 60+ | 8 | 6677.019
32 | 4 | EL8 | ok | 0 | 0 | 0 | 0 | 0 | 0 | Elevators | OK | No change | 80 | 10+ | 10 | 5425.347
32 | 4 | AXp2c | ok | 0 | 0 | 0 | 0 | 0 | 0 | Axels | OK | No change | 20 | 3.75 | 3.75 | 340.899
32 | 4 | AXp3c | ok | 0 | 0 | 0 | 0 | 0 | 0 | Axels | OK | No change | 30 | 3.75 | 3.75 | 480.15
32 | 4 | AXp3s | ok | 0 | 0 | 0 | 0 | 0 | 0 | Axels | OK | No change | 30 | 3.75 | 3.75 | 418.597
32 | 4 | AXp6s | ok | 0 | 0 | 0 | 0 | 0 | 0 | Axels | OK | No change | 60 | 3.75 | 3.75 | 838.155
32 | 4 | AXp12s | ok | 0 | 0 | 0 | 0 | 0 | 0 | Axels | OK | No change | 120 | 3.75 | 3.75 | 1677.269
32 | 4 | AXp2p | FAIL!!! |  |  |  | 0 | 0 | 0 | Axels | OK | pin change | 20 | 5 | 5 | 340.076
32 | 4 | AXp4p | ok | 0 | 0 | 0 | 0 | 0 | 0 | Axels | OK | pin change | 40 | 5 | 5 | 636.353
32 | 4 | AXb1 | ok | 0 | 0 | 0 | 0 | 0 | 0 | Axel Beams | OK | No change | 30 | 10 | 10 | 1452.922
32 | 4 | AXb3 | ok | 0 | 0 | 0 | 0 | 0 | 0 | Axel Beams | OK | No change | 30 | 30 | 10 | 2350.432
40 | 5 | MOcA_1 | ok | 5 | 5 | 5 | 15 | 100 | 40 | Motor Cases | OK | No change
40 | 5 | MOcA_2 | ok | 5 | 5 | 5 | 15 | 100 | 40 | Motor Cases | OK | No change
40 | 5 | MOhA_1 | ok | 0 | 0 | 2 | 2 | 13.33333333 | 5.333333333 | Motor Horns | OK | No change
40 | 5 | MOhA_2 | ok | 0 | 0 | 0 | 0 | 0 | 0 | Motor Horns | OK | No change
8 | 1 | BRcA_1 | ok | 0 | 0 | 0 | 0 | 0 | 0 | Brain Case | OK | many changes
8 | 1 | BRcA_2 | ok | 0 | 0 | 0 | 0 | 0 | 0 | Brain Case | OK | many changes
8 | 1 | BRcA_3 | ok | 0 | 0 | 0 | 0 | 0 | 0 | Brain Case | OK | many changes
8 | 1 | UScA_1 | ok | 0 | 0 | 0 | 0 | 0 | 0 | Ultrasonic Sensor Case | OK | add pin - low priority
8 | 1 | UScA_2 | ok | 0 | 0 | 0 | 0 | 0 | 0 | Ultrasonic Sensor Case | OK | add pin - low priority
8 | 1 | BAcA_1 | ok | 0 | 0 | 0 | 0 | 0 | 0 | AA Battery Pack Case | OK | change - copy new version as a whole part
8 | 1 | BAcA_2 | ok | 0 | 0 | 0 | 0 | 0 | 0 | AA Battery Pack Case | OK | change lower hood pin - low priority
8 | 1 | BUcA_1 | ok | 0 | 0 | 0 | 0 | 0 | 0 | Bumper 1 | OK | copy new version
8 | 1 | BUcA_2 | ok | 0 | 0 | 0 | 0 | 0 | 0 | Bumper 2 | OK | copy new version
8 | 1 | BUcA_3 | ok | 0 | 0 | 0 | 0 | 0 | 0 | Bumper 3 | OK | copy new version
 |  |  | 24.8

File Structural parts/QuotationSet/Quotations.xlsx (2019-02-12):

Company | Price (1 kit) USD | Price (1 kit) EUR | Price (1 kit) HUF | Price (100 kit) USD | Price (100 kit) EUR | Price (100 kit) HUF | Price (1 kit of 100) USD | Price (1 kit of 100) EUR | Price (1 kit of 100) HUF | Comment
The 3D Printer Experience | 205 | 180.4 | 57400 | 18011 | 15849.68 | 5043080 | 180.11 | 158.4968 | 50430.8 | https://app.fabnami.net/the3dprinterexperience/view_quote.html?workflow_id=Go9tR1Z5Vt
Varinex | 518.4 | 446.4 | 144000 | 15840 | 13640 | 4400000 | 158.4 | 136.4 | 44000
Silplast | 396 | 341 | 110000 | 20520 | 17670 | 5700000 | 205.2 | 176.7 | 57000
X-Plast | 712.5 | 625 | 198806.25 | 19950 | 17500 | 5566575 | 199.5 | 175 | 55665.75
Kvint-R |  |  |  |  |  |  | 0 | 0 | 0 | https://www.3dsystems.hu/en/contact.html
Materialise | 406.98 | 357 | 113558.13 | 13950.18 | 12237 | 3892467.33 | 139.5018 | 122.37 | 38924.6733 | https://onsite.materialise.com/en/Ordering/Quotation/440298
3D Hubs |  |  |  |  |  |  | 0 | 0 | 0 | https://www.3dhubs.com/3dprint
sculpteo | 325 | 286 | 91000 | 19327 | 17007.76 | 5411560 | 193.27 | 170.0776 | 54115.6 | https://www.sculpteo.com/en/print/2x4/tqx6LdiJ?uuid=VaIAJTch5fbtu5JEqlFjN
3D Systems | 402.42 | 353 | 112285.77 | 24795 | 21750 | 6918457.5 | 247.95 | 217.5 | 69184.575
Weerg |  |  |  |  |  |  |  |  |  | https://www.weerg.com/en/order
All3dp.com | 130 | 114.4 | 36400 | 11800 | 10384 | 3304000 | 118 | 103.84 | 33040
Greg |  |  |  | 26100 | 22968 | 7308000 | 261 | 229.68 | 73080
USD to EUR | 0.88
EUR to USD | 1.14
USD to HUF | 280
HUF to USD | 0.0036
EUR to HUF | 318.09
HUF to EUR | 0.0031

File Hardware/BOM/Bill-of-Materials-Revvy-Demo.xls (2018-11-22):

Comment | Description | Designator | LibRef | OC_Farnell | Quantity
ABT-414-RC | ABT-414-RC | Buzzer900 | Buzzer | 2098836 | 1
Capacitor 100 uF 25 V | Capacitor | C400, C401, C402, C403, C404, C405, C500, C502 | Capacitor 100 uF 25 V | 9451838 | 8
Capacitor 100 nF 0603 | Capacitor | C406, C407, C408, C409, C410, C411, C501, C600, C601, C602, C603, C700, C822, C823 | Capacitor 100 nF 0603 | 2896702 | 14
Capacitor 10 nF 0603 | Capacitor | C800, C801, C802, C803, C804, C805, C806, C807, C808, C809, C810, C811, C812, C813, C814, C815, C816, C817, C818, C819, C820, C821 | Capacitor 10 nF 0603 | 2896421 | 22
BZT52-B10X | Zener Diode | D500 | Diode_Zener_10V | 2851248 | 1
SSB44-E3/52T | Schottky Rectifier | D501 | Schottky_Diode_DO214AA | 1336557 | 1
BAT54S | Diode Schottky 30V 0.2A 3-Pin SOT-23 T/R | D800, D801, D802, D803, D804, D805, D806, D807, D808, D809, D810, D811, D812, D813, D814, D815, D816, D817, D818, D819, D820, D821, D822, D823, D824, D825, D826, D827, D828, D829, D830, D831, D832, D833 | BAT54S | 9526510 | 34
0ZCJ0200FF2C | Resistor | F500 | PolyFuse2A | 2834895 | 1
0ZCJ0050FF2G | Resistor | F501 | PolyFuse500mA | 2834889 | 1
6339160-1 | MJ,RJ45,SMT,SHLD,PANEL GRD | J200, J201, J202, J203, J204, J205 | 6339160-1 | 2059758 | 6
1-338088-3 | 8/8 INV.MOD.JACK | J206, J207, J208, J209 | 1-338088-3 | 1522228 | 4
STM32F4DISCOVERY | STM32F4DISCOVERY | J300 | STM32F4DISCOVERY_New | 2456732 | 1
WS2812B | Intelligent Control Led Integrated Light Source Pack Of 10 | LED600, LED601, LED602, LED603 | WS2812B |  | 4
FDS6681Z | P-channel MOSFET | Q500 | P FET FDS6681Z | 1611454 | 1
Value | N Chanel mosfet | Q900 | 2N7002 | 9845313 | 1
Resistor_10k | Resistor | R500, R900 | Resistor_10k | 2059627 | 2
Resistor_2K2 | Resistor | R600 | Resistor_2K2 | 2908362 | 1
Resistor_4k7 | Resistor | R800, R808 | Resistor_4k7 | 2059619 | 2
Resistor_1k | Resistor | R801, R802, R804, R805, R806, R807, R810, R811, R812, R814, R815, R816, R817, R818, R819, R820, R822, R823, R824, R825, R827, R828, R829, R830, R831, R832, R834, R835, R836, R837 | Resistor_1k | 2059601 | 30
Resistor_100 | Resistor | R803, R809, R901 | Resistor_100 | 2303059 | 3
Resistor_3K | Resistor | R813, R821, R826, R833 | Resistor_3K | 2073461 | 4
Resistor_18K | Resistor | R838, R840 | Resistor_18K | 2447269 | 2
Resistor_2K | Resistor | R839, R841 | Resistor_2K | 2447319 | 2
L202011MS02Q | DPDT Switch | SW500 | Switch_L202011MS02Q | 2320074 | 1
Value | IC - VNH7070 | U400, U401, U402, U403, U404, U405 | IC - VNH7070 | 2797973 | 6
LM3940IMP-3.3 | 1A Low Dropout Regulator for 5V to 3.3V Conversion 4-SOT-223 -40 to 125 | U500 | LM3940IMP-3.3 | 1469104 | 1
HC-05 | HC-05 | U700 | HC-05_Stand |  | 1
LPCR035CTP | Lightpipe |  |  | 2832150 | 4

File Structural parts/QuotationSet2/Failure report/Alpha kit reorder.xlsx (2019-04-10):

RRF Part # | Qty | Part Type
S4x1 | 18 | Straight Beams
S8x1 | 4 | Straight Beams
S12x1 | 21 | Straight Beams
S4x2 | 10 | Straight Beams
S24x2 | 7 | Straight Beams
S4x3 | 4 | Straight Beams
S4x4 | 32 | Straight Beams
S8x4 | 13 | Straight Beams
A135 | 32 | Angled Beams
A90L | 54 | Angled Beams
A90T | 64 | Angled Beams
CB4H | 24 | Curved Beams
CT2x2 | 16 | Connector Triangle
CC1x1 | 32 | Connector Cubes
CC2x2 | 78 | Connector Cubes
G40 | 32 | Gears
G60 | 32 | Gears
AXp2p | Ordered in a previous e-mail | Axels
MOcA_1 | 40 | Motor Cases
MOcA_2 | 40 | Motor Cases
MOhA_1 | 7 | Motor Horns

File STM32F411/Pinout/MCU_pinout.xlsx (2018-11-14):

Position | Name | Type | Signal | Label | Comment
92 | PB6 | I/O | I2C1_SCL | Audio_SCL [CS43L22_SCL]
25 | PA2 | I/O | ADC1_IN2 | BAT1 [ADC_IN2]
26 | PA3 | I/O | ADC1_IN3 | BAT2 [ADC_IN3]
5 | PE6 | I/O | TIM9_CH2 | BUZZER_PWM [TIM9_CH2]
64 | PC7 | I/O | USART6_RX | HM-10 [USART6 RX] | Bluetooth
63 | PC6 | I/O | USART6_TX | HM-10 [USART6 TX] | Bluetooth
61 | PD14 | Output | GPIO_Output | LD5 [Red Led]
62 | PD15 | Output | GPIO_Output | LD6 [Blue Led]
51 | PB12 | Input | GPIO_Input | LEFT1_ENC_B
81 | PD0 | I/O | GPIO_EXTI0 | LEFT1_EXTI0 | ENC_A
54 | PB15 | Output | GPIO_Output | LEFT1_FW
40 | PE9 | I/O | TIM1_CH1 | LEFT1_PWM [TIM1_CH1]
58 | PD11 | Output | GPIO_Output | LEFT1_RW
52 | PB13 | Input | GPIO_Input | LEFT2_ENC_B
82 | PD1 | I/O | GPIO_EXTI1 | LEFT2_EXTI1 | ENC_A
7 | PC13-ANTI_TAMP | Output | GPIO_Output | LEFT2_FW
42 | PE11 | I/O | TIM1_CH2 | LEFT2_PWM [TIM1_CH2]
8 | PC14-OSC32_IN | Output | GPIO_Output | LEFT2_RW
53 | PB14 | Input | GPIO_Input | LEFT3_ENC_B
83 | PD2 | I/O | GPIO_EXTI2 | LEFT3_EXTI2 | ENC_A
78 | PC10 | Output | GPIO_Output | LEFT3_FW
44 | PE13 | I/O | TIM1_CH3 | LEFT3_PWM [TIM1_CH3]
79 | PC11 | Output | GPIO_Output | LEFT3_RW
12 | PH0 - OSC_IN | I/O | RCC_OSC_IN | PH0-OSC_IN
13 | PH1 - OSC_OUT | I/O | RCC_OSC_OUT | PH1-OSC_OUT
38 | PE7 | Input | GPIO_Input | RIGHT1_ENC_B
84 | PD3 | I/O | GPIO_EXTI3 | RIGHT1_EXTI3 | ENC_A
31 | PA6 | Output | GPIO_Output | RIGHT1_FW
45 | PE14 | I/O | TIM1_CH4 | RIGHT1_PWM [TIM1_CH4]
32 | PA7 | Output | GPIO_Output | RIGHT1_RW
39 | PE8 | Input | GPIO_Input | RIGHT2_ENC_B
85 | PD4 | I/O | GPIO_EXTI4 | RIGHT2_EXTI4 | ENC_A
68 | PA9 | Output | GPIO_Output | RIGHT2_FW
77 | PA15 | I/O | TIM2_CH1 | RIGHT2_PWM [TIM2_CH1]
69 | PA10 | Output | GPIO_Output | RIGHT2_RW
57 | PD10 | Input | GPIO_Input | RIGHT3_ENC_B
86 | PD5 | I/O | GPIO_EXTI5 | RIGHT3_EXTI5 | ENC_A
59 | PD12 | Output | GPIO_Output | RIGHT3_FW [Green Led]
47 | PB10 | I/O | TIM2_CH3 | RIGHT3_PWM [TIM2_CH3]
60 | PD13 | Output | GPIO_Output | RIGHT3_RW [Orange Led]
15 | PC0 | I/O | ADC1_IN10 | SEN1 [ADC_IN10]
87 | PD6 | I/O | GPIO_EXTI6 | SEN1_EXTI | Ultrasonic echo
29 | PA4 | Output | GPIO_Output | SEN1_OUT | Ultrasonic trigger
16 | PC1 | I/O | ADC1_IN11 | SEN2 [ADC_IN11]
88 | PD7 | I/O | GPIO_EXTI7 | SEN2_EXTI | Ultrasonic echo
30 | PA5 | Output | GPIO_Output | SEN2_OUT | Ultrasonic trigger
17 | PC2 | I/O | ADC1_IN12 | SEN3 [ADC_IN12]
55 | PD8 | I/O | GPIO_EXTI8 | SEN3_EXTI | Ultrasonic echo
33 | PC4 | Output | GPIO_Output | SEN3_OUT | Ultrasonic trigger
18 | PC3 | I/O | ADC1_IN13 | SEN4 [ADC_IN13]
56 | PD9 | I/O | GPIO_EXTI9 | SEN4_EXTI | Ultrasonic echo
34 | PC5 | Output | GPIO_Output | SEN4_OUT | Ultrasonic trigger
67 | PA8 | I/O | I2C3_SCL | SENSOR_SCL [I2C3]
66 | PC9 | I/O | I2C3_SDA | SENSOR_SDA [I2C3]
90 | PB4 | I/O | TIM3_CH1 | SERVO1 [TIM3_CH1] | Left1
91 | PB5 | I/O | TIM3_CH2 | SERVO2 [TIM3_CH2] | Left2
35 | PB0 | I/O | TIM3_CH3 | SERVO3 [TIM3_CH3] | Left3
36 | PB1 | I/O | TIM3_CH4 | SERVO4 [TIM3_CH4] | Right1
23 | PA0-WKUP | I/O | TIM5_CH1 | SERVO5 [TIM5_CH1] | Right2
24 | PA1 | I/O | TIM5_CH2 | SERVO6 [TIM5_CH2] | Right3
76 | PA14 | I/O | SYS_JTCK-SWCLK | SWCLK
72 | PA13 | I/O | SYS_JTMS-SWDIO | SWDIO
89 | PB3 | I/O | SYS_JTDO-SWO | SWO
~~93~~ | ~~PB7~~ | ~~I/O~~ | ~~TIM4_CH2~~ | ~~WS2812_PWM [TIM4_CH2]~~ | ~~Neopixel LEDs~~
96 | PB9 | I/O | I2C1_SDA
70 | PA11 | I/O | USB_OTG_FS_DM
71 | PA12 | I/O | USB_OTG_FS_DP
1 | PE2 | I/O
2 | PE3 | I/O
3 | PE4 | I/O
4 | PE5 | I/O
6 | VBAT | Power
9 | PC15-OSC32_OUT | I/O
10 | VSS | Power
11 | VDD | Power
14 | NRST | Reset
19 | VDD | Power
20 | VSSA | Power
21 | VREF+ | Power
22 | VDDA | Power
27 | VSS | Power
28 | VDD | Power
37 | PB2 | I/O
41 | PE10 | I/O
43 | PE12 | I/O
46 | PE15 | I/O
48 | VCAP1 | Power
49 | VSS | Power
50 | VDD | Power
65 | PC8 | I/O
73 | VCAP2 | Power
74 | VSS | Power
75 | VDD | Power
80 | PC12 | I/O
94 | BOOT0 | Boot
95 | PB8 | I/O | SPI5_MOSI | WS2812 [SPI5_MOSI] | Neopixel LEDs
97 | PE0 | I/O
98 | PE1 | I/O
99 | VSS | Power
100 | VDD | Power

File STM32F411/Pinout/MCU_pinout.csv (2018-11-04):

Position | Name | Type | Signal | Label
1 | PE2 | I/O
2 | PE3 | I/O
3 | PE4 | I/O
4 | PE5 | I/O
5 | PE6 | I/O | TIM9_CH2 | BUZZER_PWM [TIM9_CH2]
6 | VBAT | Power
7 | PC13-ANTI_TAMP | Output | GPIO_Output | LEFT2_FW
8 | PC14-OSC32_IN | Output | GPIO_Output | LEFT2_RW
9 | PC15-OSC32_OUT | I/O
10 | VSS | Power
11 | VDD | Power
12 | PH0 - OSC_IN | I/O | RCC_OSC_IN | PH0-OSC_IN
13 | PH1 - OSC_OUT | I/O | RCC_OSC_OUT | PH1-OSC_OUT
14 | NRST | Reset
15 | PC0 | I/O | ADC1_IN10 | SEN1 [ADC_IN10]
16 | PC1 | I/O | ADC1_IN11 | SEN2 [ADC_IN11]
17 | PC2 | I/O | ADC1_IN12 | SEN3 [ADC_IN12]
18 | PC3 | I/O | ADC1_IN13 | SEN4 [ADC_IN13]
19 | VDD | Power
20 | VSSA | Power
21 | VREF+ | Power
22 | VDDA | Power
23 | PA0-WKUP | I/O | TIM5_CH1 | SERVO5 [TIM5_CH1]
24 | PA1 | I/O | TIM5_CH2 | SERVO6 [TIM5_CH2]
25 | PA2 | I/O | ADC1_IN2 | BAT1 [ADC_IN2]
26 | PA3 | I/O | ADC1_IN3 | BAT2 [ADC_IN3]
27 | VSS | Power
28 | VDD | Power
29 | PA4 | Output | GPIO_Output | SEN1_OUT
30 | PA5 | Output | GPIO_Output | SEN2_OUT
31 | PA6 | Output | GPIO_Output | RIGHT1_FW
32 | PA7 | Output | GPIO_Output | RIGHT1_RW
33 | PC4 | Output | GPIO_Output | SEN3_OUT
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

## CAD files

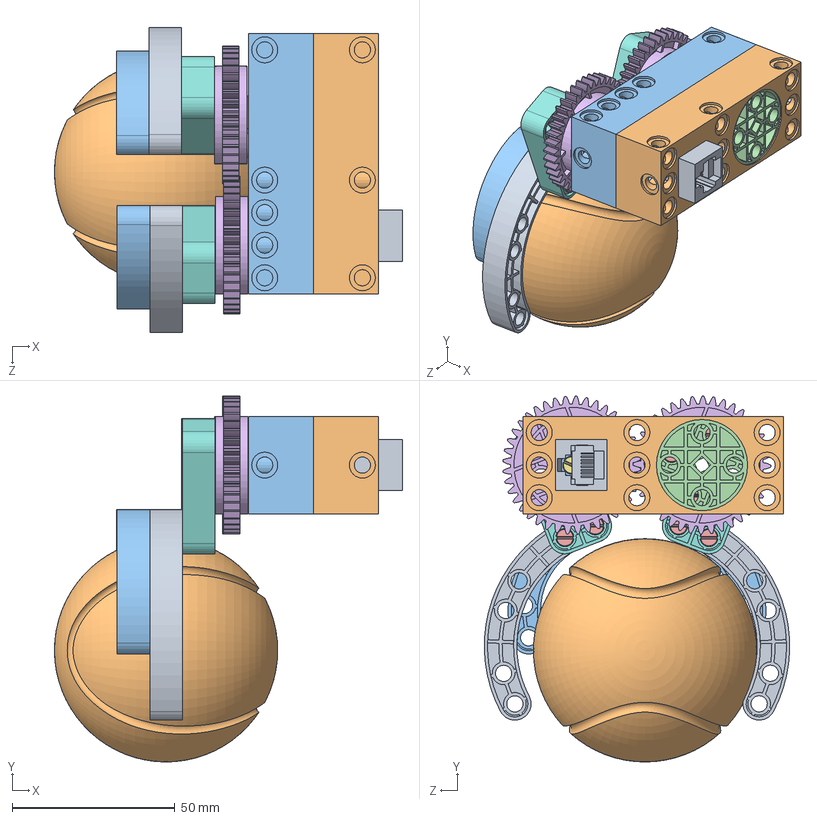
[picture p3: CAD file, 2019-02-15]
Structural parts/Demo parts/Claw demo/claw_v2.SLDASM
107.0 x 112.4 x 93.8 mm
rj45_vert
Rotor x 2
CP1x1 x 9
G40 x 2
AXp2p
S4x2 x 2
CB6H x 2
tennis ball
CB4H x 2

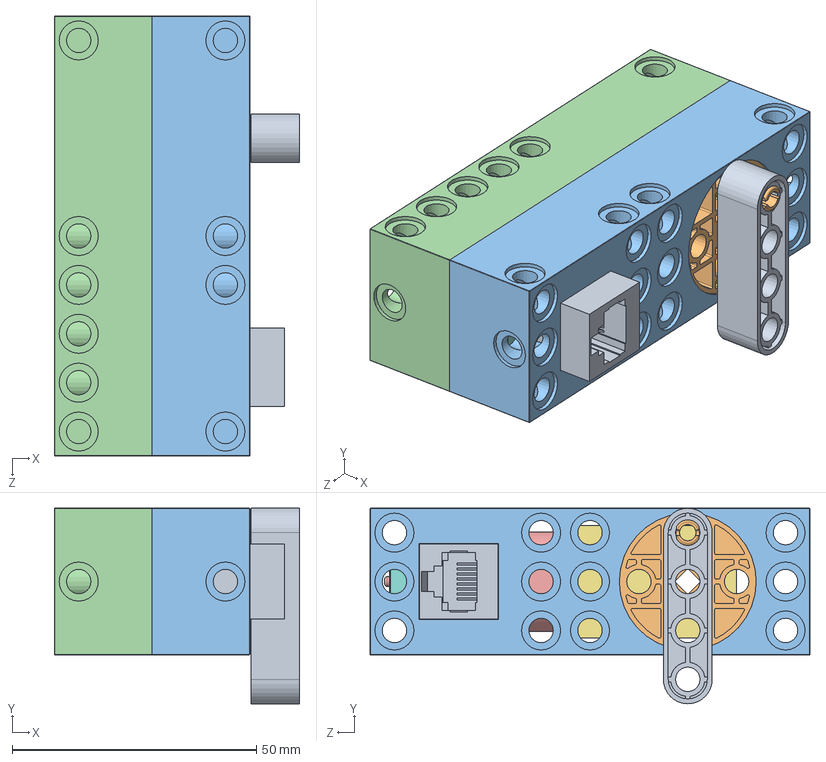
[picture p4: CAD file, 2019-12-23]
Structural parts/Demo parts/Motor 2_/MObeta.SLDASM
50.2 x 40.0 x 90.0 mm
RJ45x1A
MOhA x 2
MOcA_1
MOcA_2
MOdc6VA
Magnet_ring^MObeta
gearbox^MObeta
PCB^MObeta

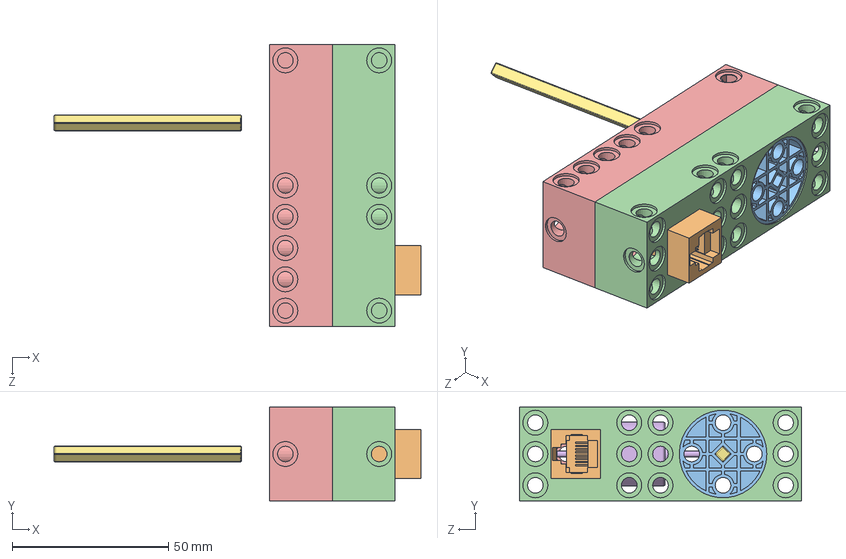
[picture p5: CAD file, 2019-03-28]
Structural parts/Demo parts/Motor_/motor_axle2.SLDASM
117.3 x 30.0 x 90.0 mm
rj45_vert
MOhA x 2
MOcA_1
MOcA_2
ff130-13200
AXp6s

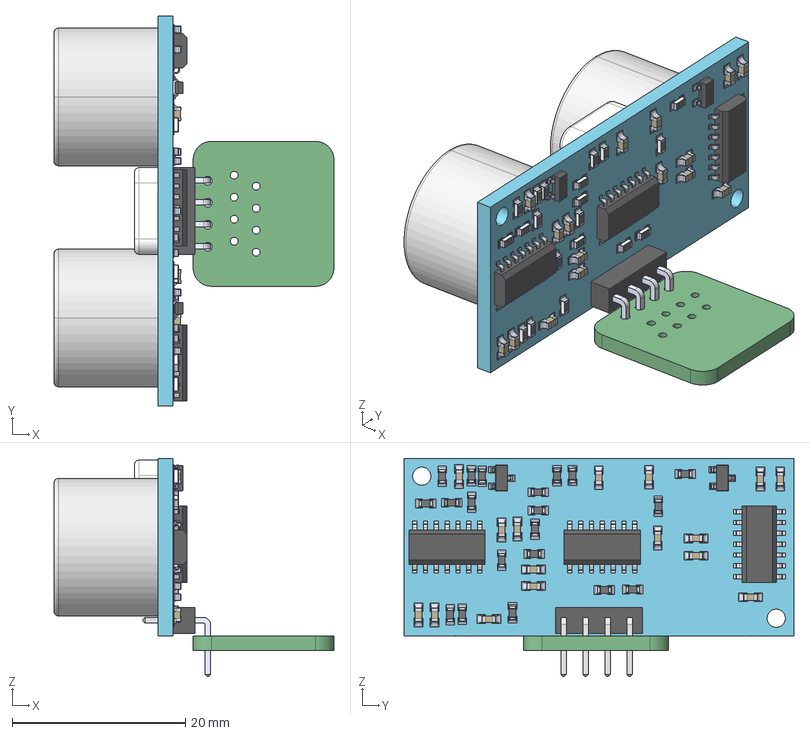
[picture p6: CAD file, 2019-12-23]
Structural parts/Demo parts/Ultrasonic sensor/HC-SR04_fullPCB.step
32.3 x 45.0 x 25.2 mm
Board
User_Library-HC-SR04_PCB
User_Library-HC-SR04_Transducer x 2
User_Library-HC-SR04_3_Pin_Header_90_Degree
User_Library-HC-SR04_14_Pin_SMT x 3
User_Library-HC-SR04_HC-SR04_Crystal.SLDASM
User_Library-HC-SR04_ssot3 x 2
User_Library-HC-SR04_MLC0603 x 20
User_Library-HC-SR04_603_cap_on_pad x 16

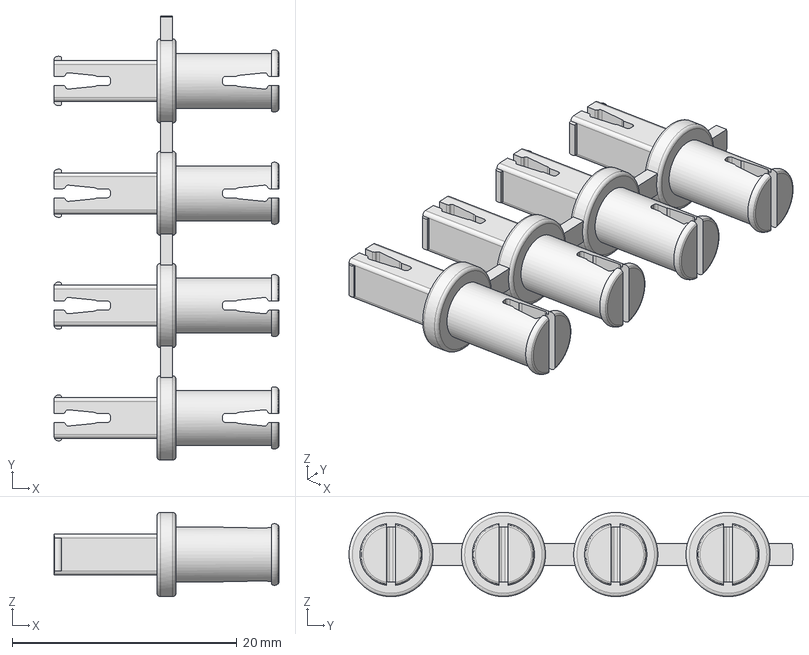
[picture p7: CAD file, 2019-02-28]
Structural parts/RFQ/SLS print collection Rev 1/AXp2p/AXp2p test assembly.stp
20.0 x 39.5 x 7.50 mm

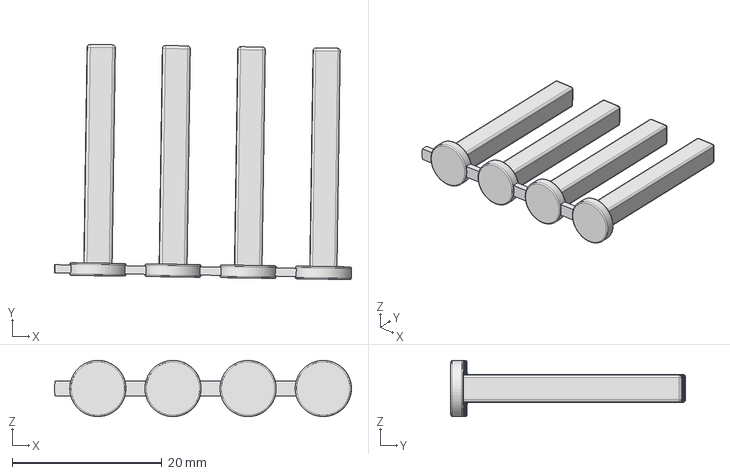
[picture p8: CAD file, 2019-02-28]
Structural parts/RFQ/SLS print collection Rev 1/AXp3c/AXp3c test assembly.stp
39.6 x 31.4 x 7.50 mm

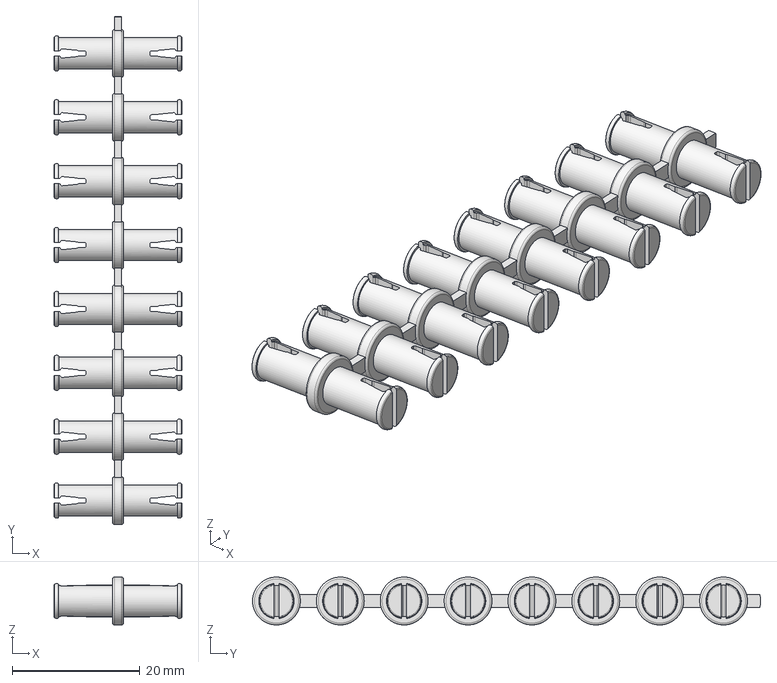
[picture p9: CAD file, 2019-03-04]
Structural parts/RFQ/SLS print collection Rev 1/CP1x1/CP1x1 test assembly.stp
20.0 x 79.5 x 7.50 mm

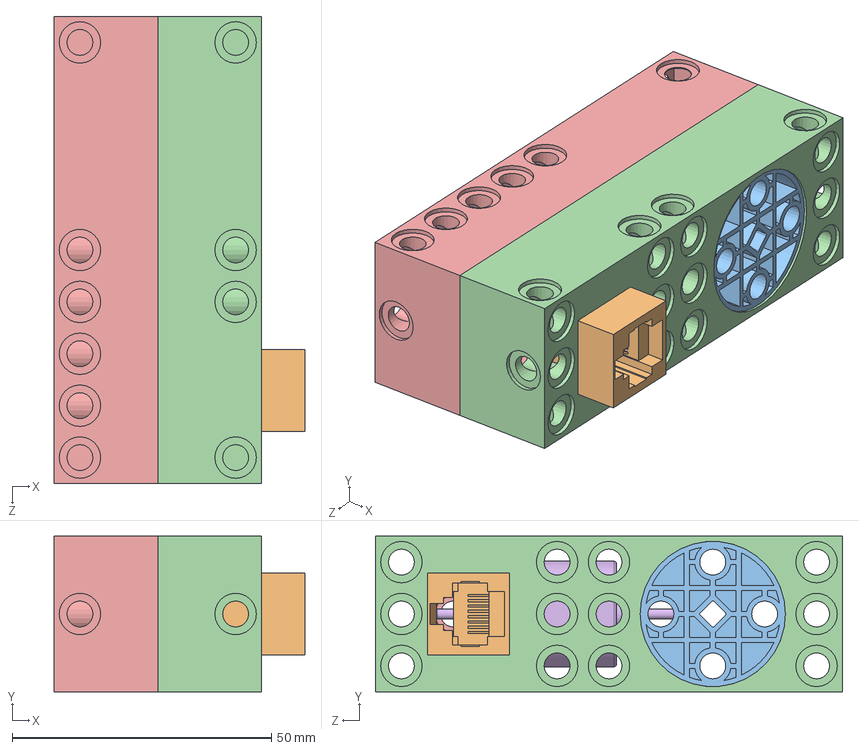
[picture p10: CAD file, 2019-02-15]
Structural parts/Demo parts/Battery2/motor.SLDASM
48.4 x 30.0 x 90.0 mm
rj45_vert
MOhA x 2
MOcA_1
MOcA_2
ff130-13200

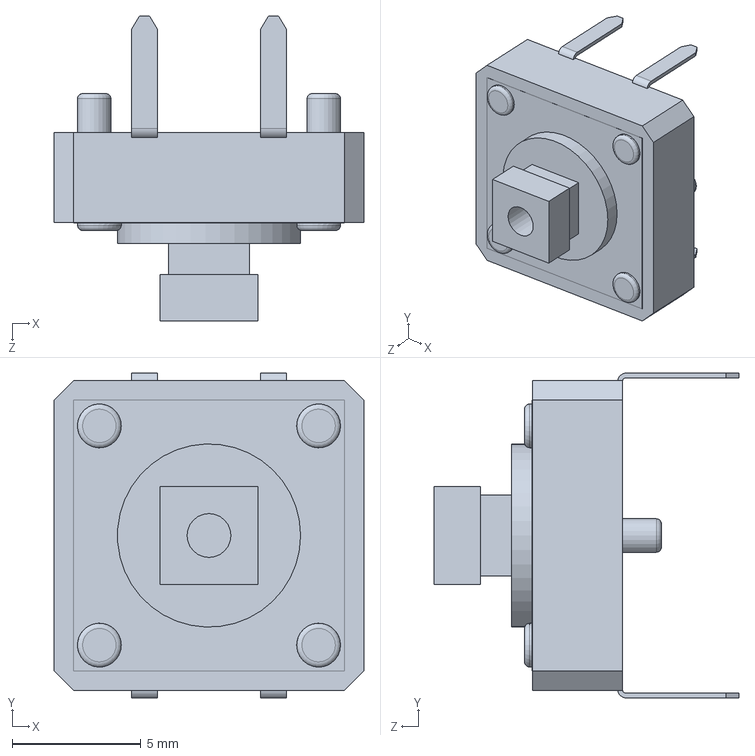
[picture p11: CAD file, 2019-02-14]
Structural parts/Demo parts/Bumper/SWITCH.SLDASM
12.0 x 12.6 x 11.8 mm

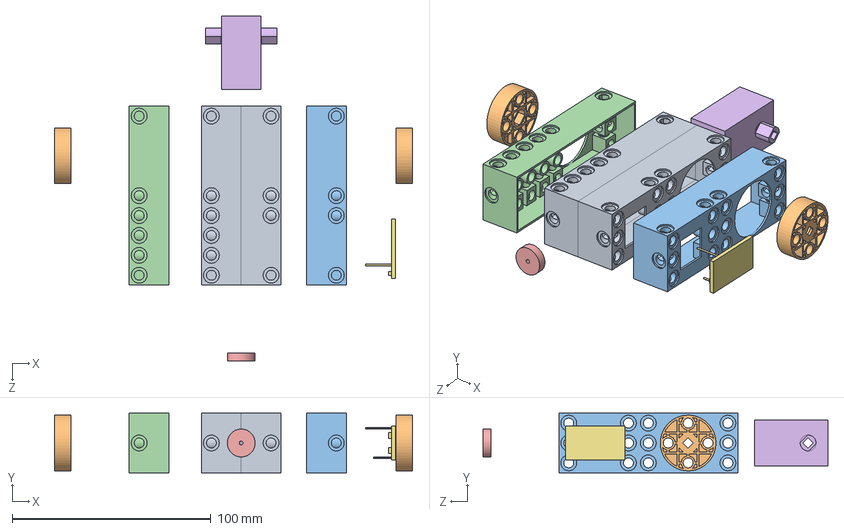
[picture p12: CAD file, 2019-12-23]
Structural parts/Demo parts/Motor 2_/motor_expl.SLDASM
180.0 x 30.0 x 173.4 mm
MOhA x 2
MOcA_1
MOcA_2
Magnet_ring^motor_expl
gearbox^motor_expl
PCB^motor_expl

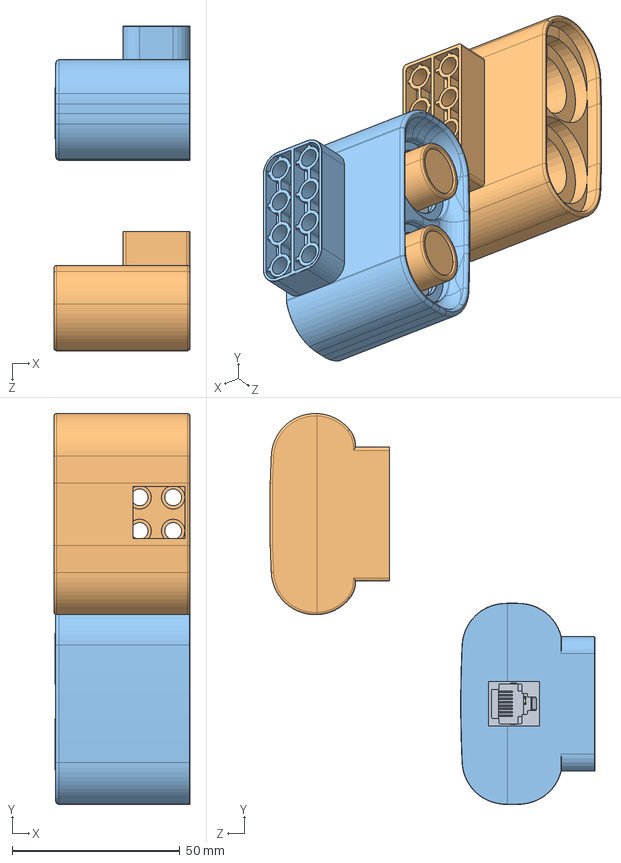
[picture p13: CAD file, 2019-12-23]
Structural parts/Demo parts/Ultrasonic sensor 2/HC-SR04_assembly.SLDASM
40.5 x 116.5 x 96.8 mm
User_Library-HC-SR04_PCB.step
User_Library-HC-SR04_Transducer.step x 2
User_Library-HC-SR04_3_Pin_Header_90_Degree.step
User_Library-HC-SR04_14_Pin_SMT.step x 3
User_Library-HC-SR04_HC-SR04_Crystal.SLDASM.step
User_Library-HC-SR04_ssot3.step x 2
User_Library-HC-SR04_MLC0603.step x 20
User_Library-HC-SR04_603_cap_on_pad.step x 16
rj45_144-L
UScA_final
Board.step

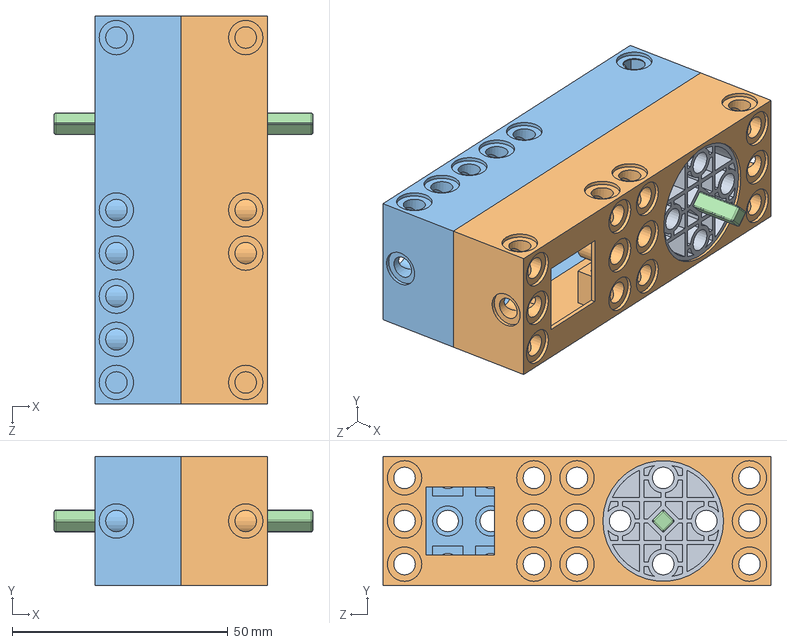
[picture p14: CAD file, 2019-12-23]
Structural parts/Demo parts/Motor 2_/motor_axle1.SLDASM
60.0 x 30.0 x 90.0 mm
MOhA x 2
MOcA_1
MOcA_2
AXp6s

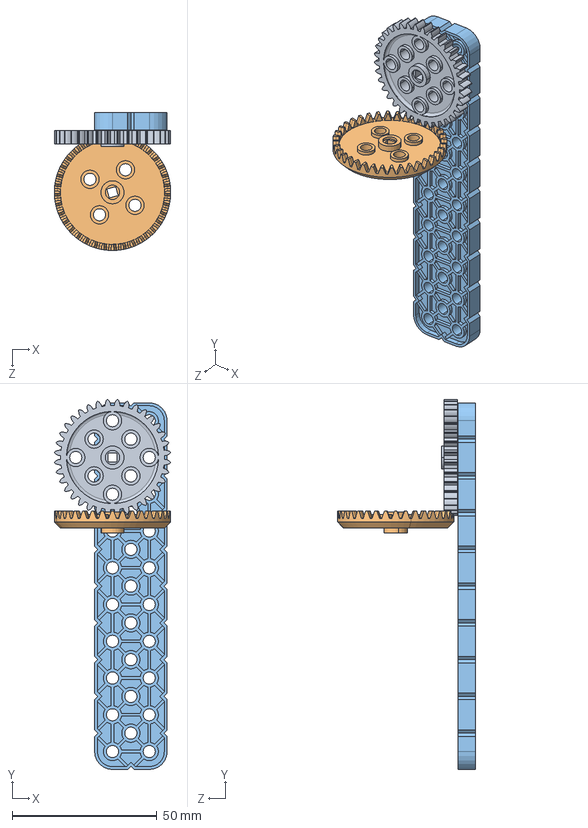
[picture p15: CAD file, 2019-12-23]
Structural parts/Gears/VEX Gearboxes/CrownTest.SLDASM
40.2 x 127.8 x 47.7 mm
MediumGear_228-2500-214
Crown_228-2500-218

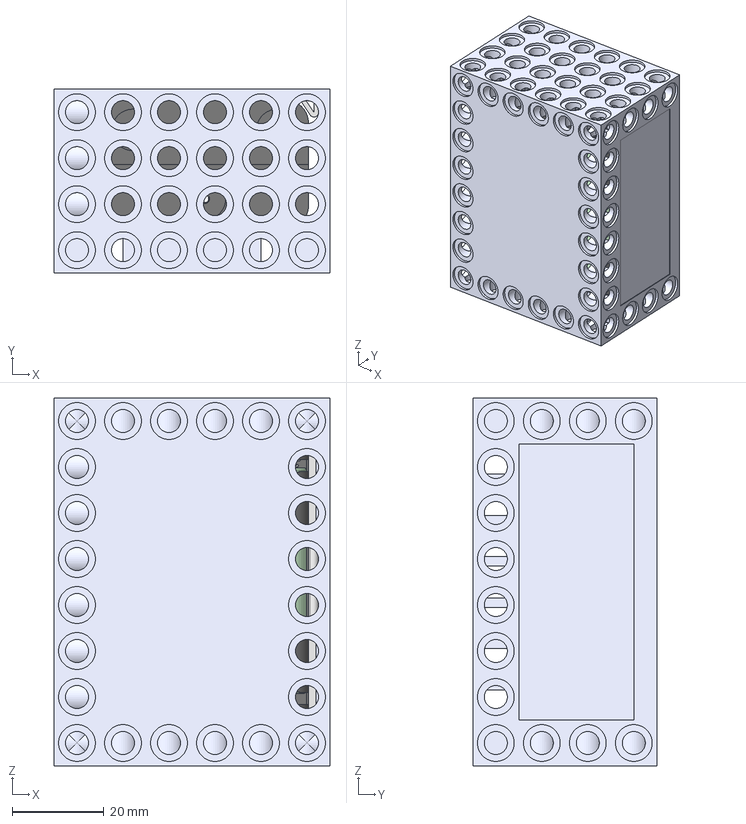
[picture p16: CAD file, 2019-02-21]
Structural parts/RFQ/20190221/Battery/BAcA_assembly.stp
60.0 x 40.1 x 80.0 mm
BAcA
Battery_holder_WZY-148-1
Battery x 6
BAcA_3

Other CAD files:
Structural parts/Demo parts/Brain/U405.sldasm
Structural parts/Demo parts/Brain/D811.sldasm
Structural parts/Demo parts/Brain/U401.sldasm
Structural parts/Demo parts/Brain/U404.sldasm
Structural parts/Axle Connectors/Axle connector 3x3 cross.ipt
Structural parts/Axles/AXp2+c.ipt
Structural parts/Axles/AXp2+c/AXp2c.ipt
Structural parts/Axles/AXp2+c/AXp2c.stl
Structural parts/Axles/AXp2+c/AXp3c.ipt
Structural parts/Axles/AXp2+c/AXp3c.stl
Structural parts/Axles/AXp2+s.ipt
Structural parts/Axles/AXp2+s/AXp12s.ipt
Structural parts/Axles/AXp2+s/AXp3s.ipt
Structural parts/Axles/AXp2+s/AXp3s.stl
Structural parts/Axles/AXp2+s/AXp6s.ipt
Structural parts/Axles/AXp2+s/AXp6s.stl
Structural parts/Axles/AXp2p.iam
Structural parts/Axles/AXp2p.ipt
Structural parts/Axles/AXp2p.stl
Structural parts/Axles/AXp2p.stp
Structural parts/Axles/AXp3+p.iam
Structural parts/Axles/AXp3+p/AXp3p.iam
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

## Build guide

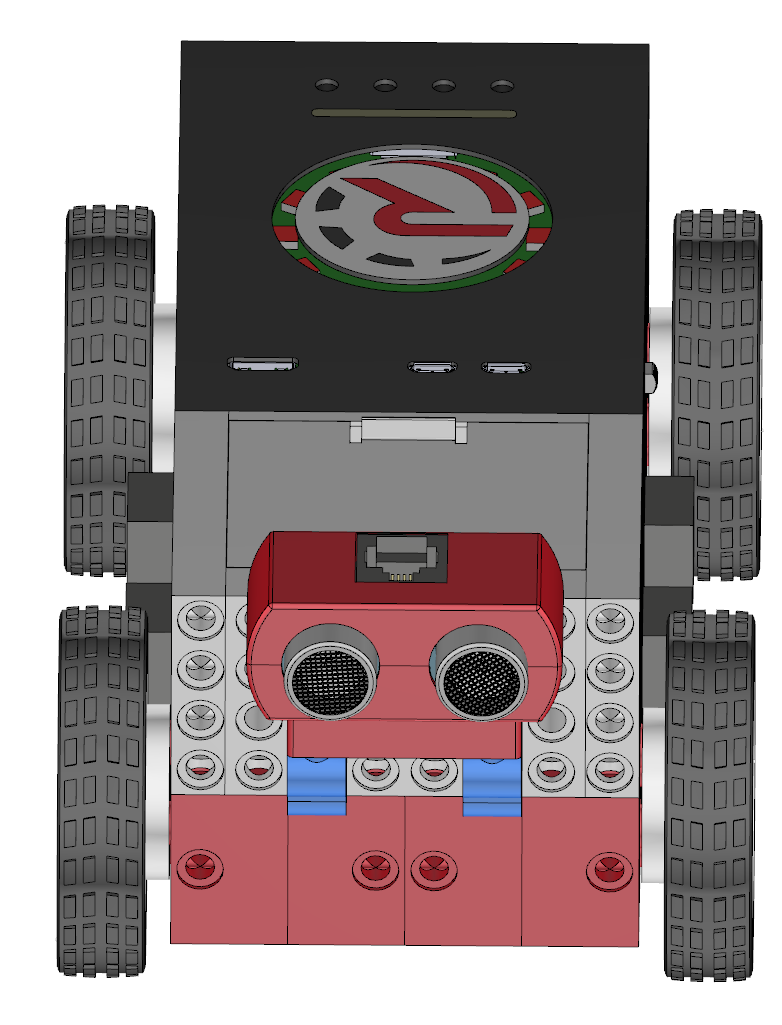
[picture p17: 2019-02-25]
Structural parts/Demonstrations/UltraSonic Assembly/UltraSonic Assembly 3.png

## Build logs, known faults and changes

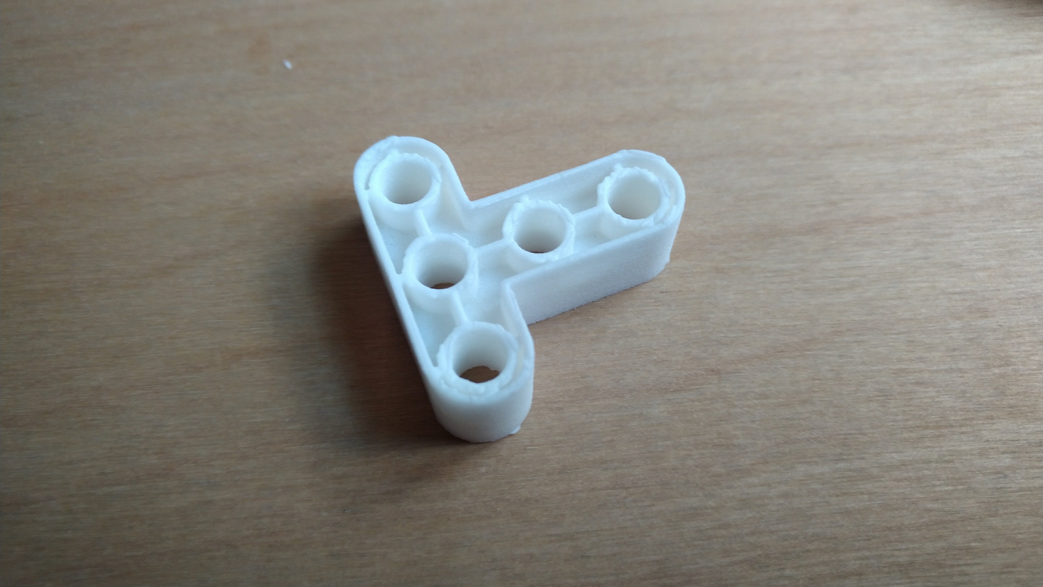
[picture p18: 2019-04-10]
Structural parts/QuotationSet2/Failure report/A90T.jpg

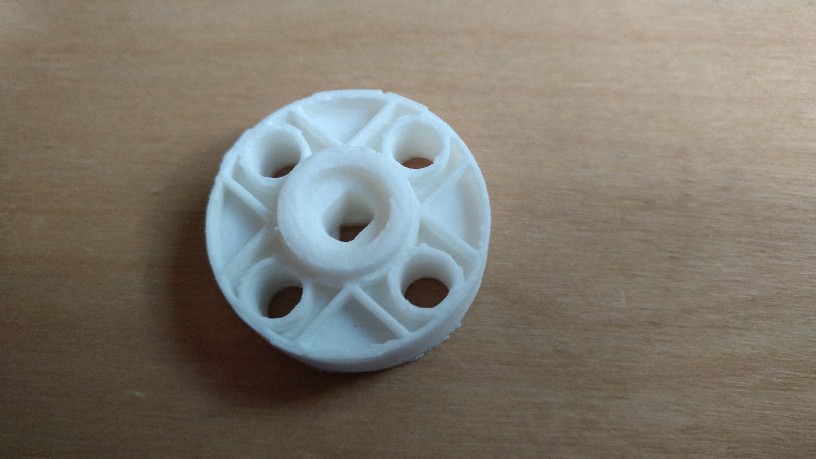
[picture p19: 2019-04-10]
Structural parts/QuotationSet2/Failure report/MOhA_1.jpg

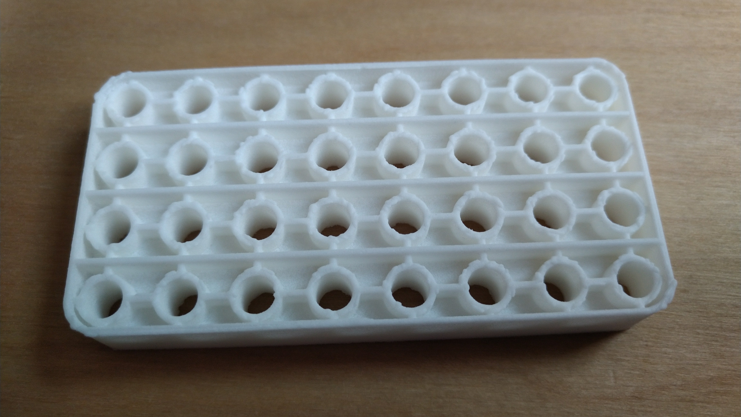
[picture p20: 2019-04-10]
Structural parts/QuotationSet2/Failure report/S8x4.jpg

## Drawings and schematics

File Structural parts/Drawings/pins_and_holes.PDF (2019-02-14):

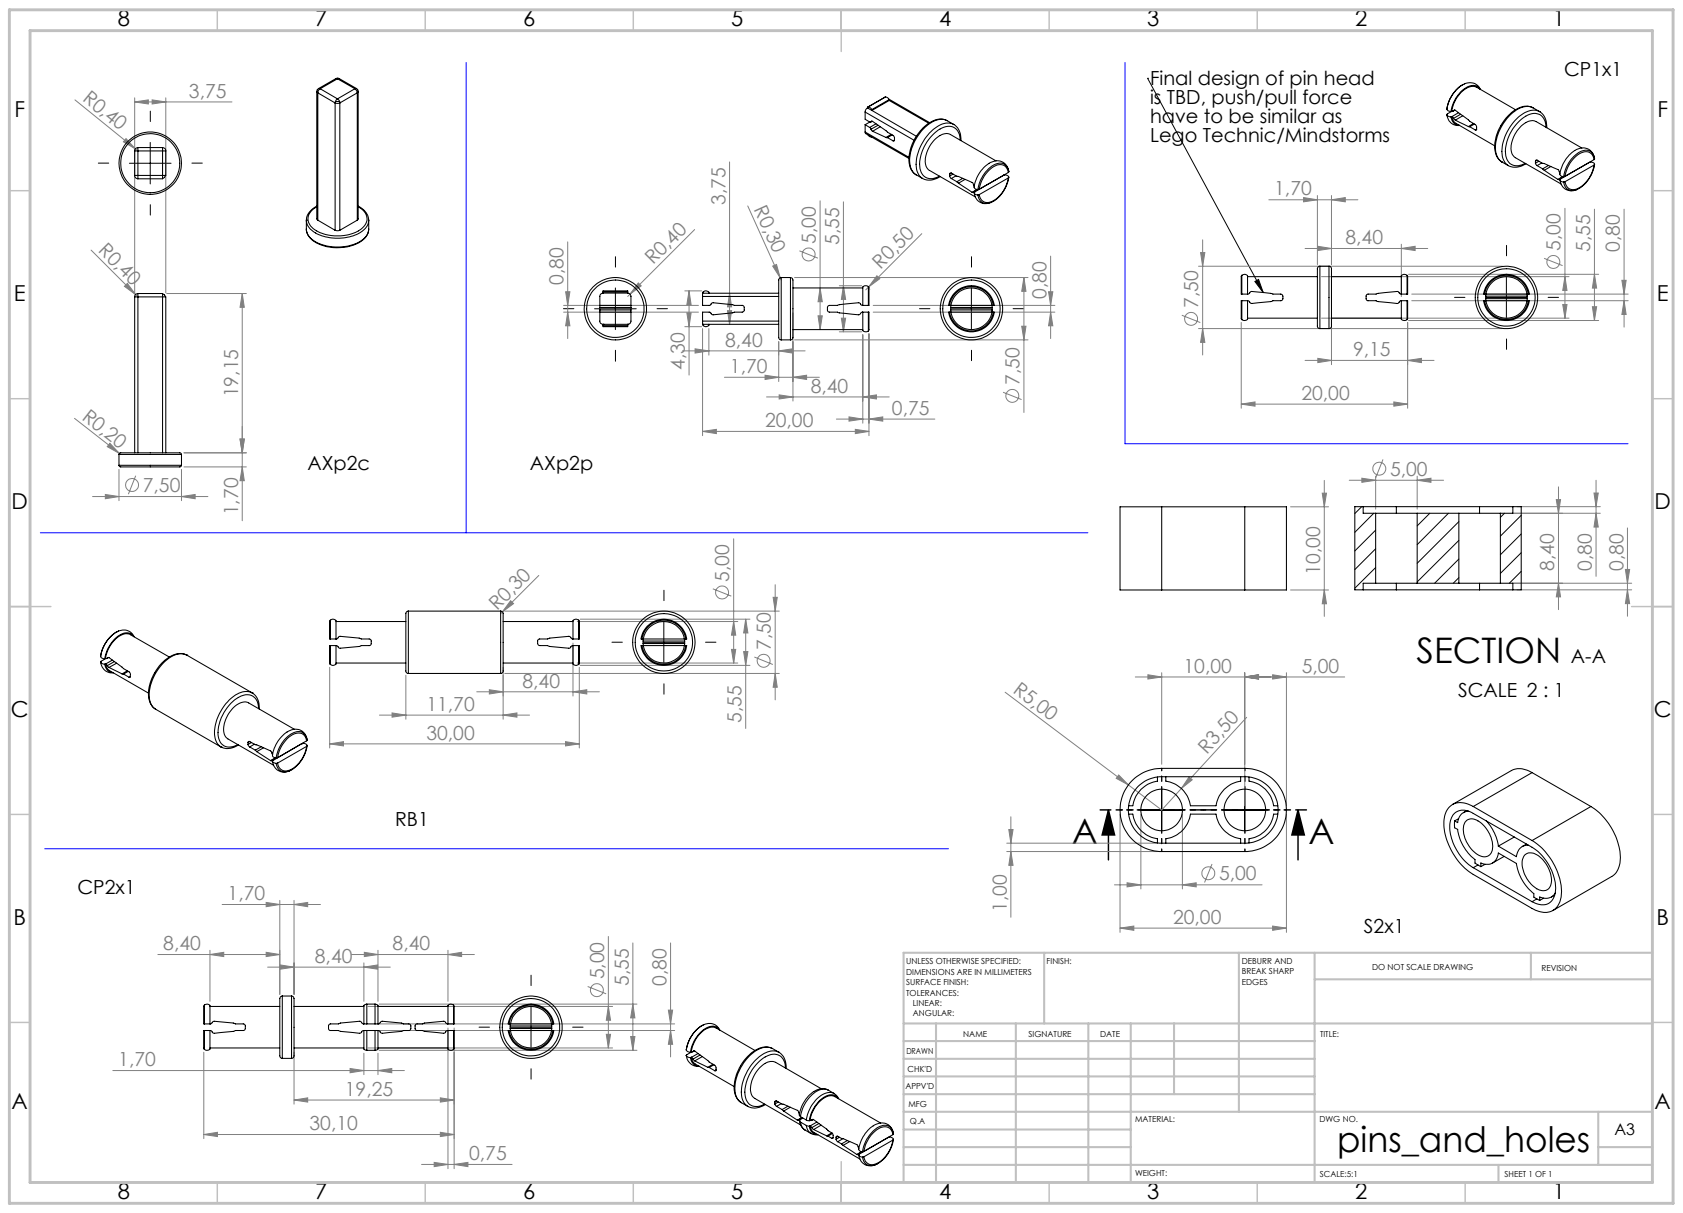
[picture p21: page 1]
SECTION A-A; SCALE 2 : 1 11,70; FINISH:; DEBURR AND; BREAK SHARP; DO NOT SCALE DRAWING; REVISION; SCALE:5:1; SHEET 1 OF 1

Final design of pin head
is TBD, push/pull force
have to be similar as
Lego Technic/Mindstorms 7,50

UNLESS OTHERWISE SPECIFIED:
DIMENSIONS ARE IN MILLIMETERS
SURFACE FINISH:
TOLERANCES:
LINEAR:
ANGULAR:

NAME | SIGNATURE | DATE | | | | TITLE:

DRAWN
CHK'D
APPV'D
MFG
Q.A | | | | MATERIAL: | DWG NO. pins_and_holes | A3

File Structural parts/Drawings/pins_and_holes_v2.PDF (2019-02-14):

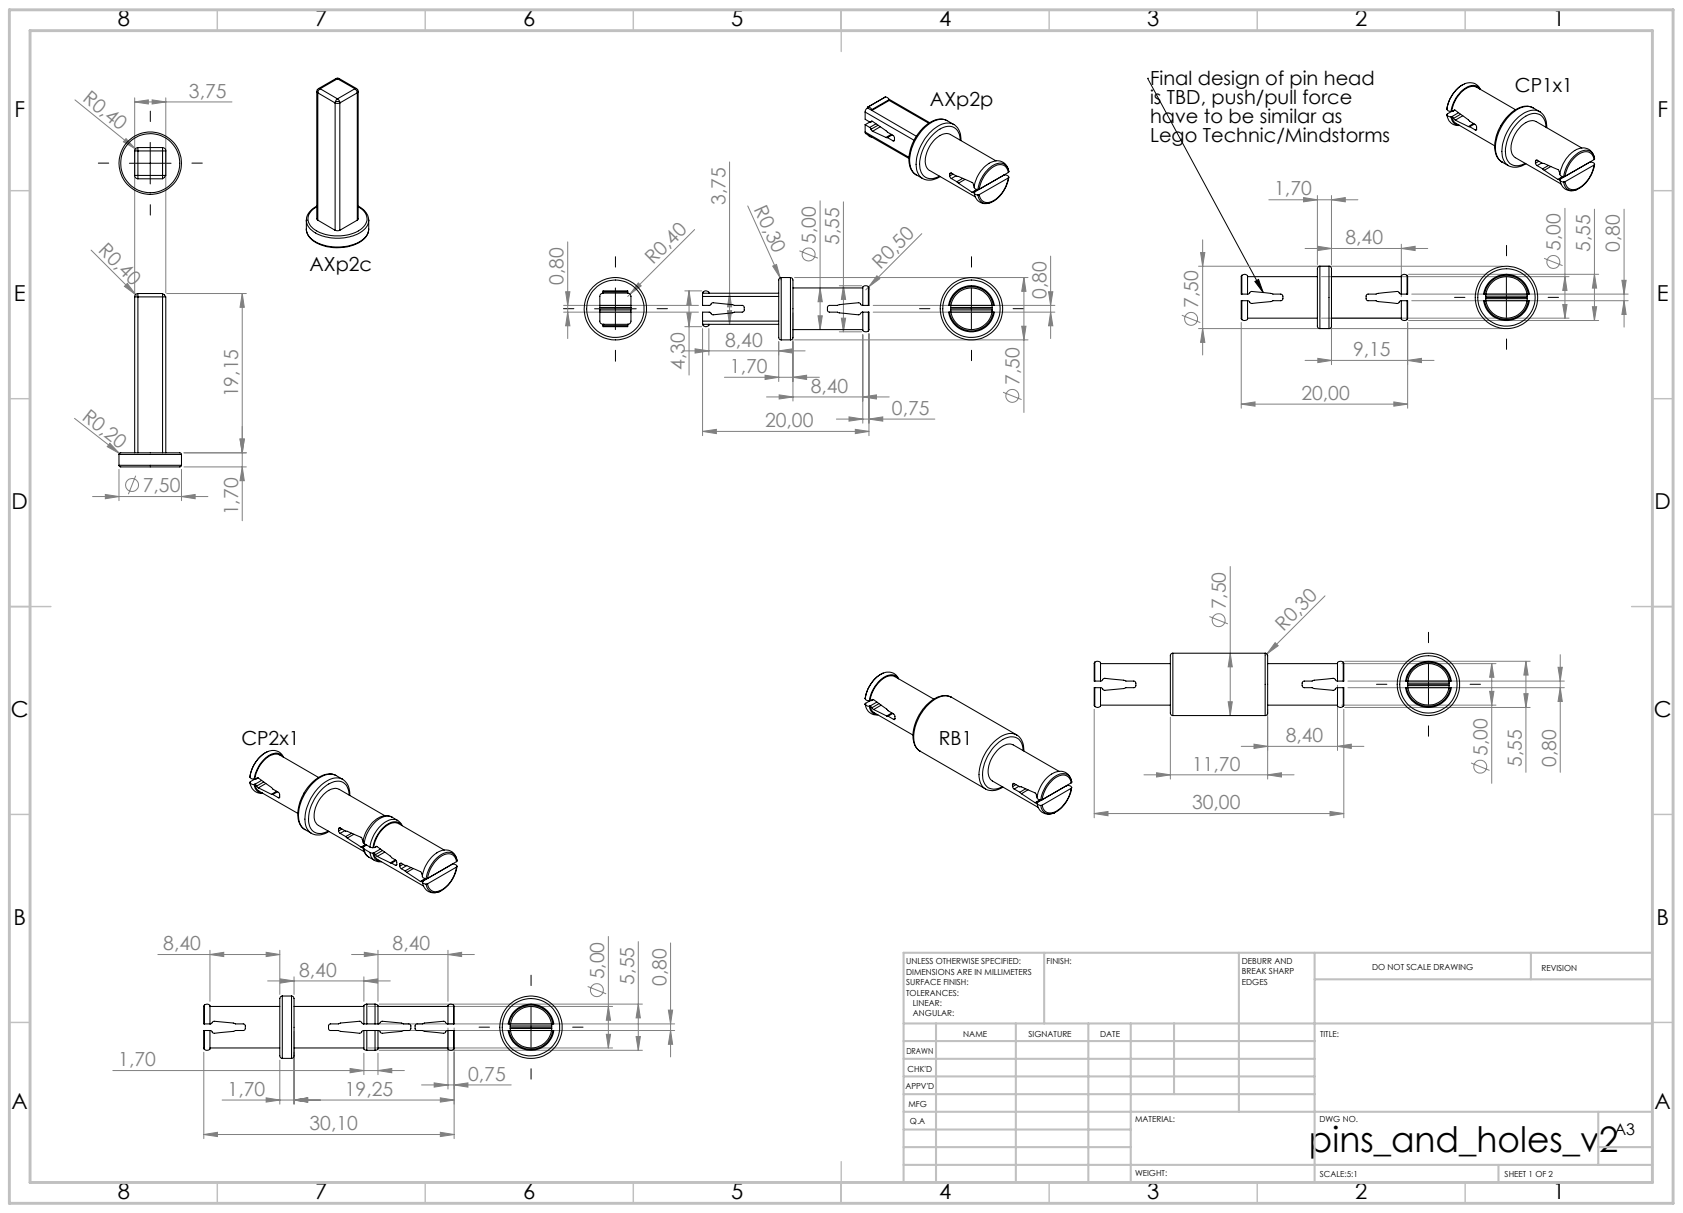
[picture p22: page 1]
FINISH:; DEBURR AND; BREAK SHARP; DO NOT SCALE DRAWING; REVISION; SCALE:5:1; SHEET 1 OF 2

Final design of pin head
is TBD, push/pull force
have to be similar as
Lego Technic/Mindstorms 7,50

UNLESS OTHERWISE SPECIFIED:
DIMENSIONS ARE IN MILLIMETERS
SURFACE FINISH:
TOLERANCES:
LINEAR:
ANGULAR:

NAME | SIGNATURE | DATE | | | | TITLE:

DRAWN
CHK'D
APPV'D
MFG
Q.A | | | | MATERIAL: pins_and_holes_v2 | DWG NO. | A3

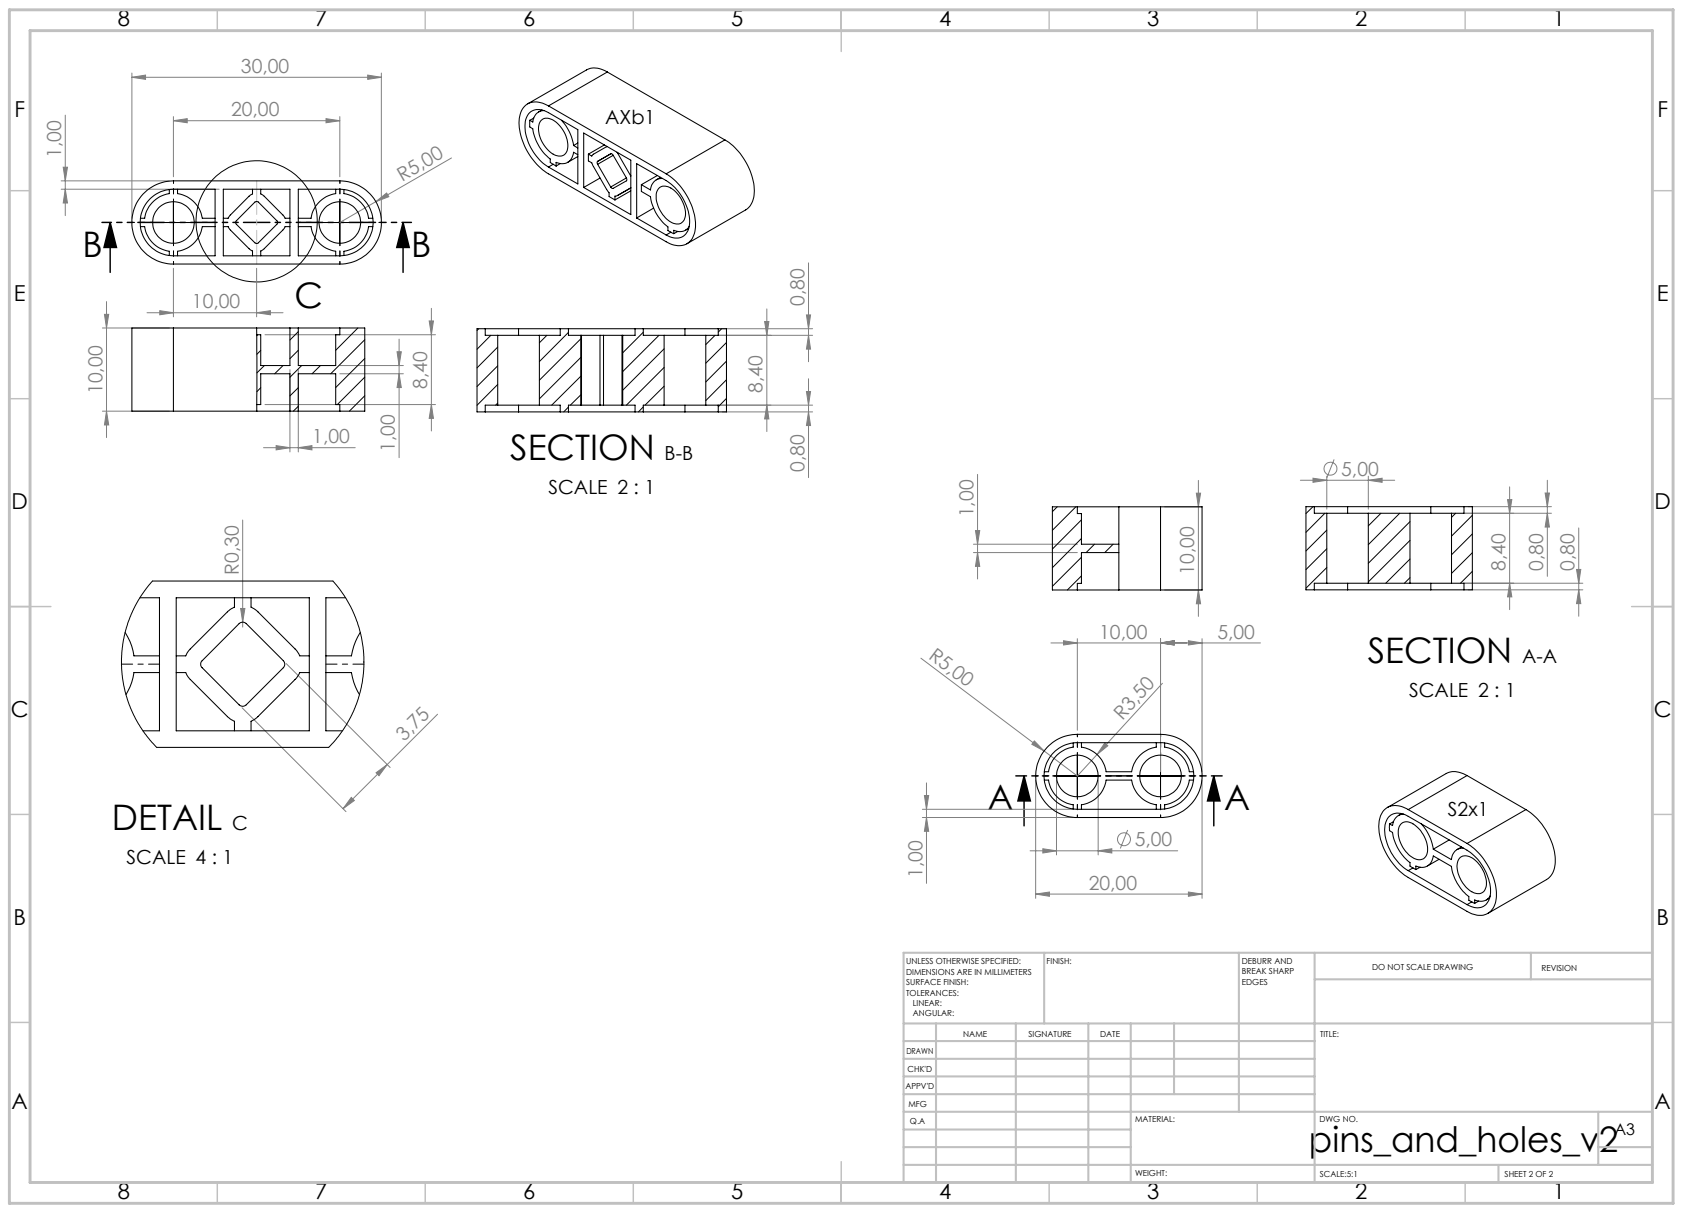
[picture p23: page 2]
SECTION B-B; SCALE 2 : 1; DETAIL C; SCALE 4 : 1; SECTION A-A; FINISH:; DEBURR AND; BREAK SHARP; DO NOT SCALE DRAWING; REVISION; SCALE:5:1; SHEET 2 OF 2

UNLESS OTHERWISE SPECIFIED:
DIMENSIONS ARE IN MILLIMETERS
SURFACE FINISH:
TOLERANCES:
LINEAR:
ANGULAR:

NAME | SIGNATURE | DATE | | | | TITLE:

DRAWN
CHK'D
APPV'D
MFG
Q.A | | | | MATERIAL: pins_and_holes_v2 | DWG NO. | A3

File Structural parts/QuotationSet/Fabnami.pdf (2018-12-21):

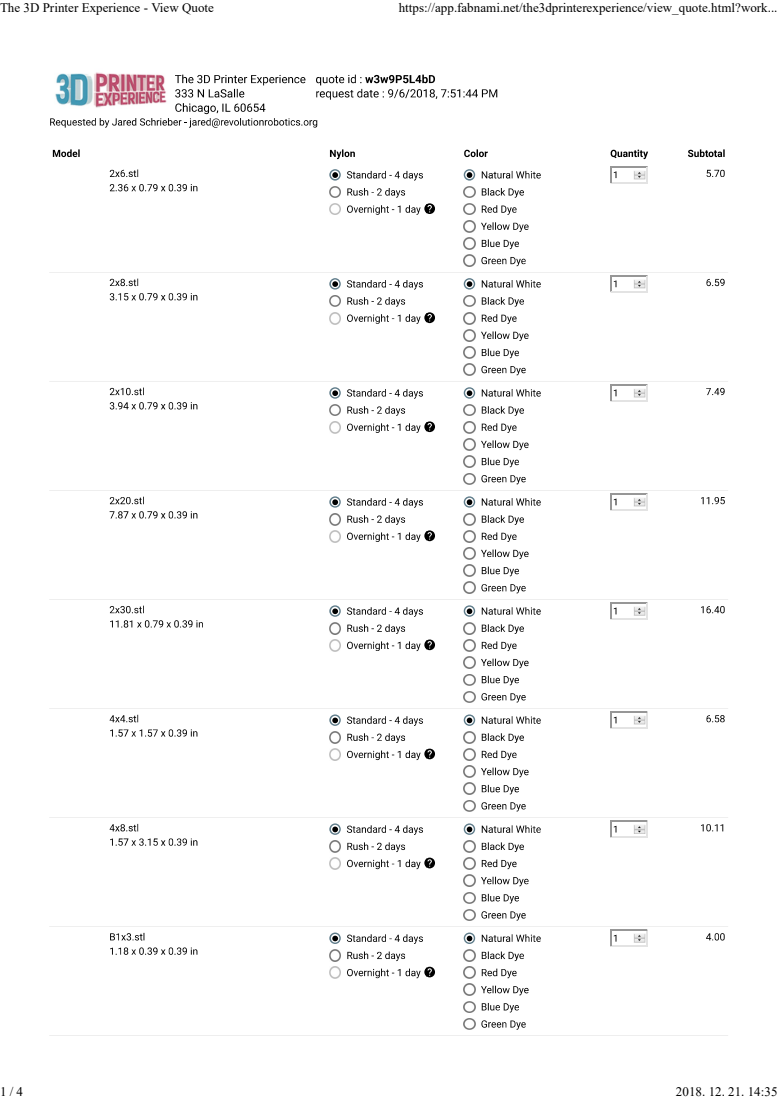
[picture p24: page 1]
The 3D Printer Experience - View Quote; https://app.fabnami.net/the3dprinterexperience/view_quote.html?work...

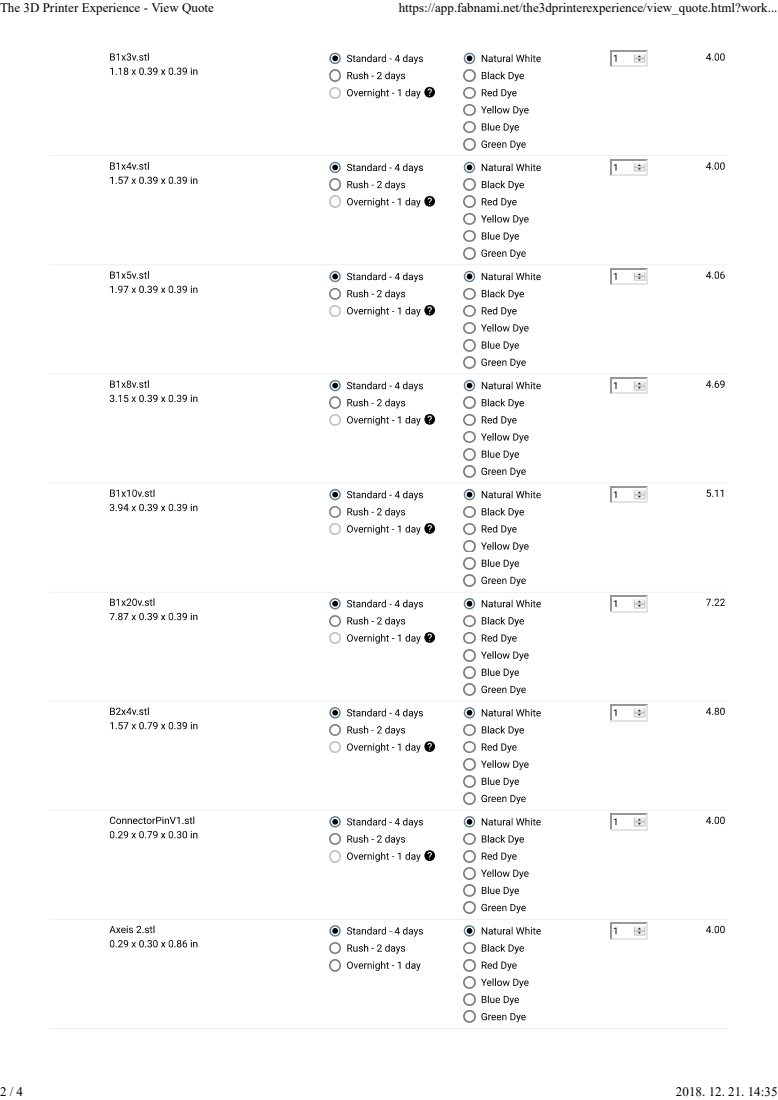
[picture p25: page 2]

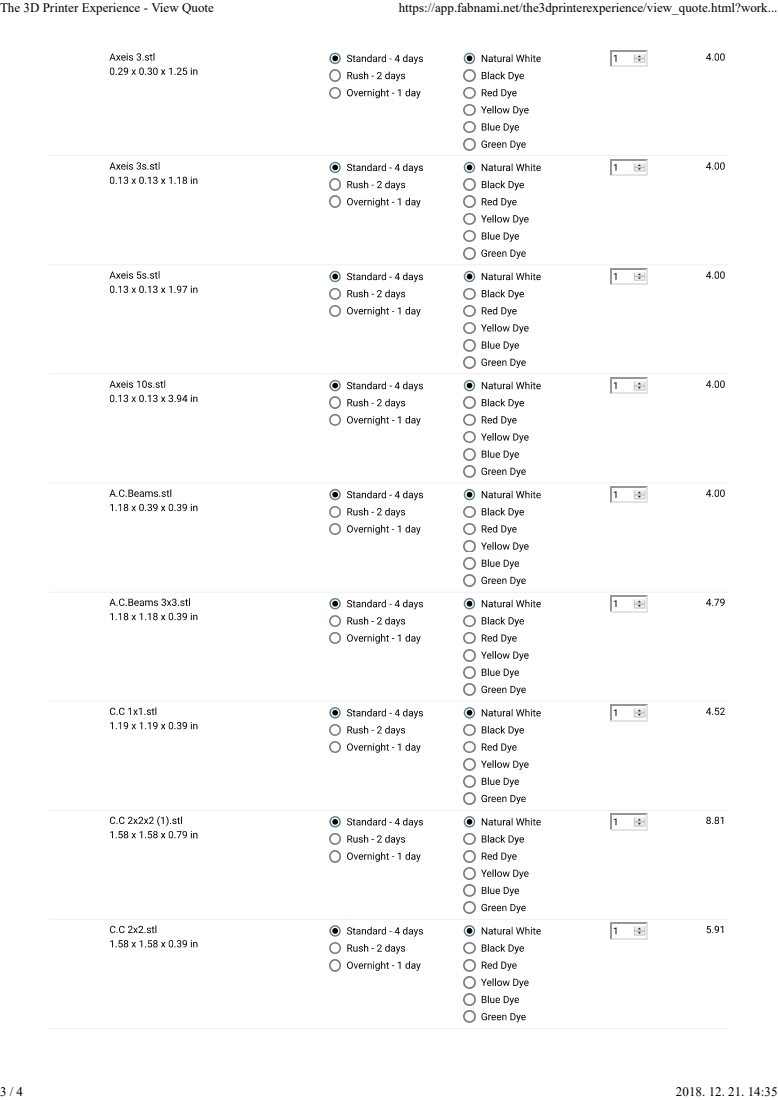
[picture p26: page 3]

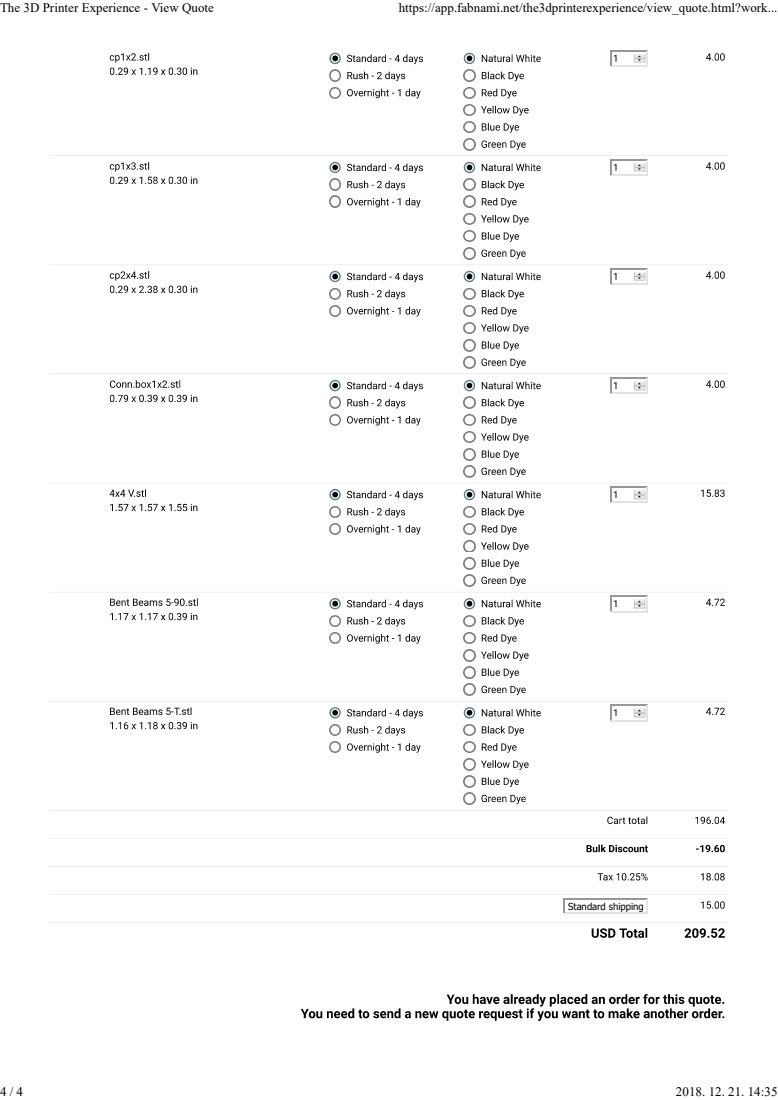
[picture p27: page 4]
Standard shipping

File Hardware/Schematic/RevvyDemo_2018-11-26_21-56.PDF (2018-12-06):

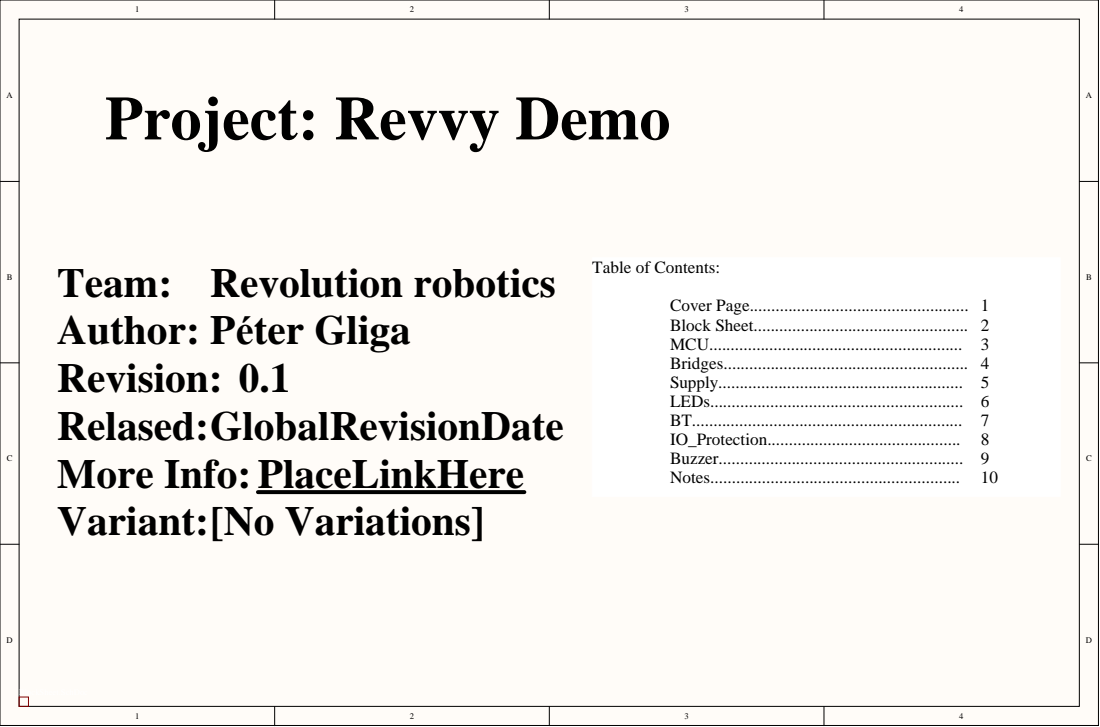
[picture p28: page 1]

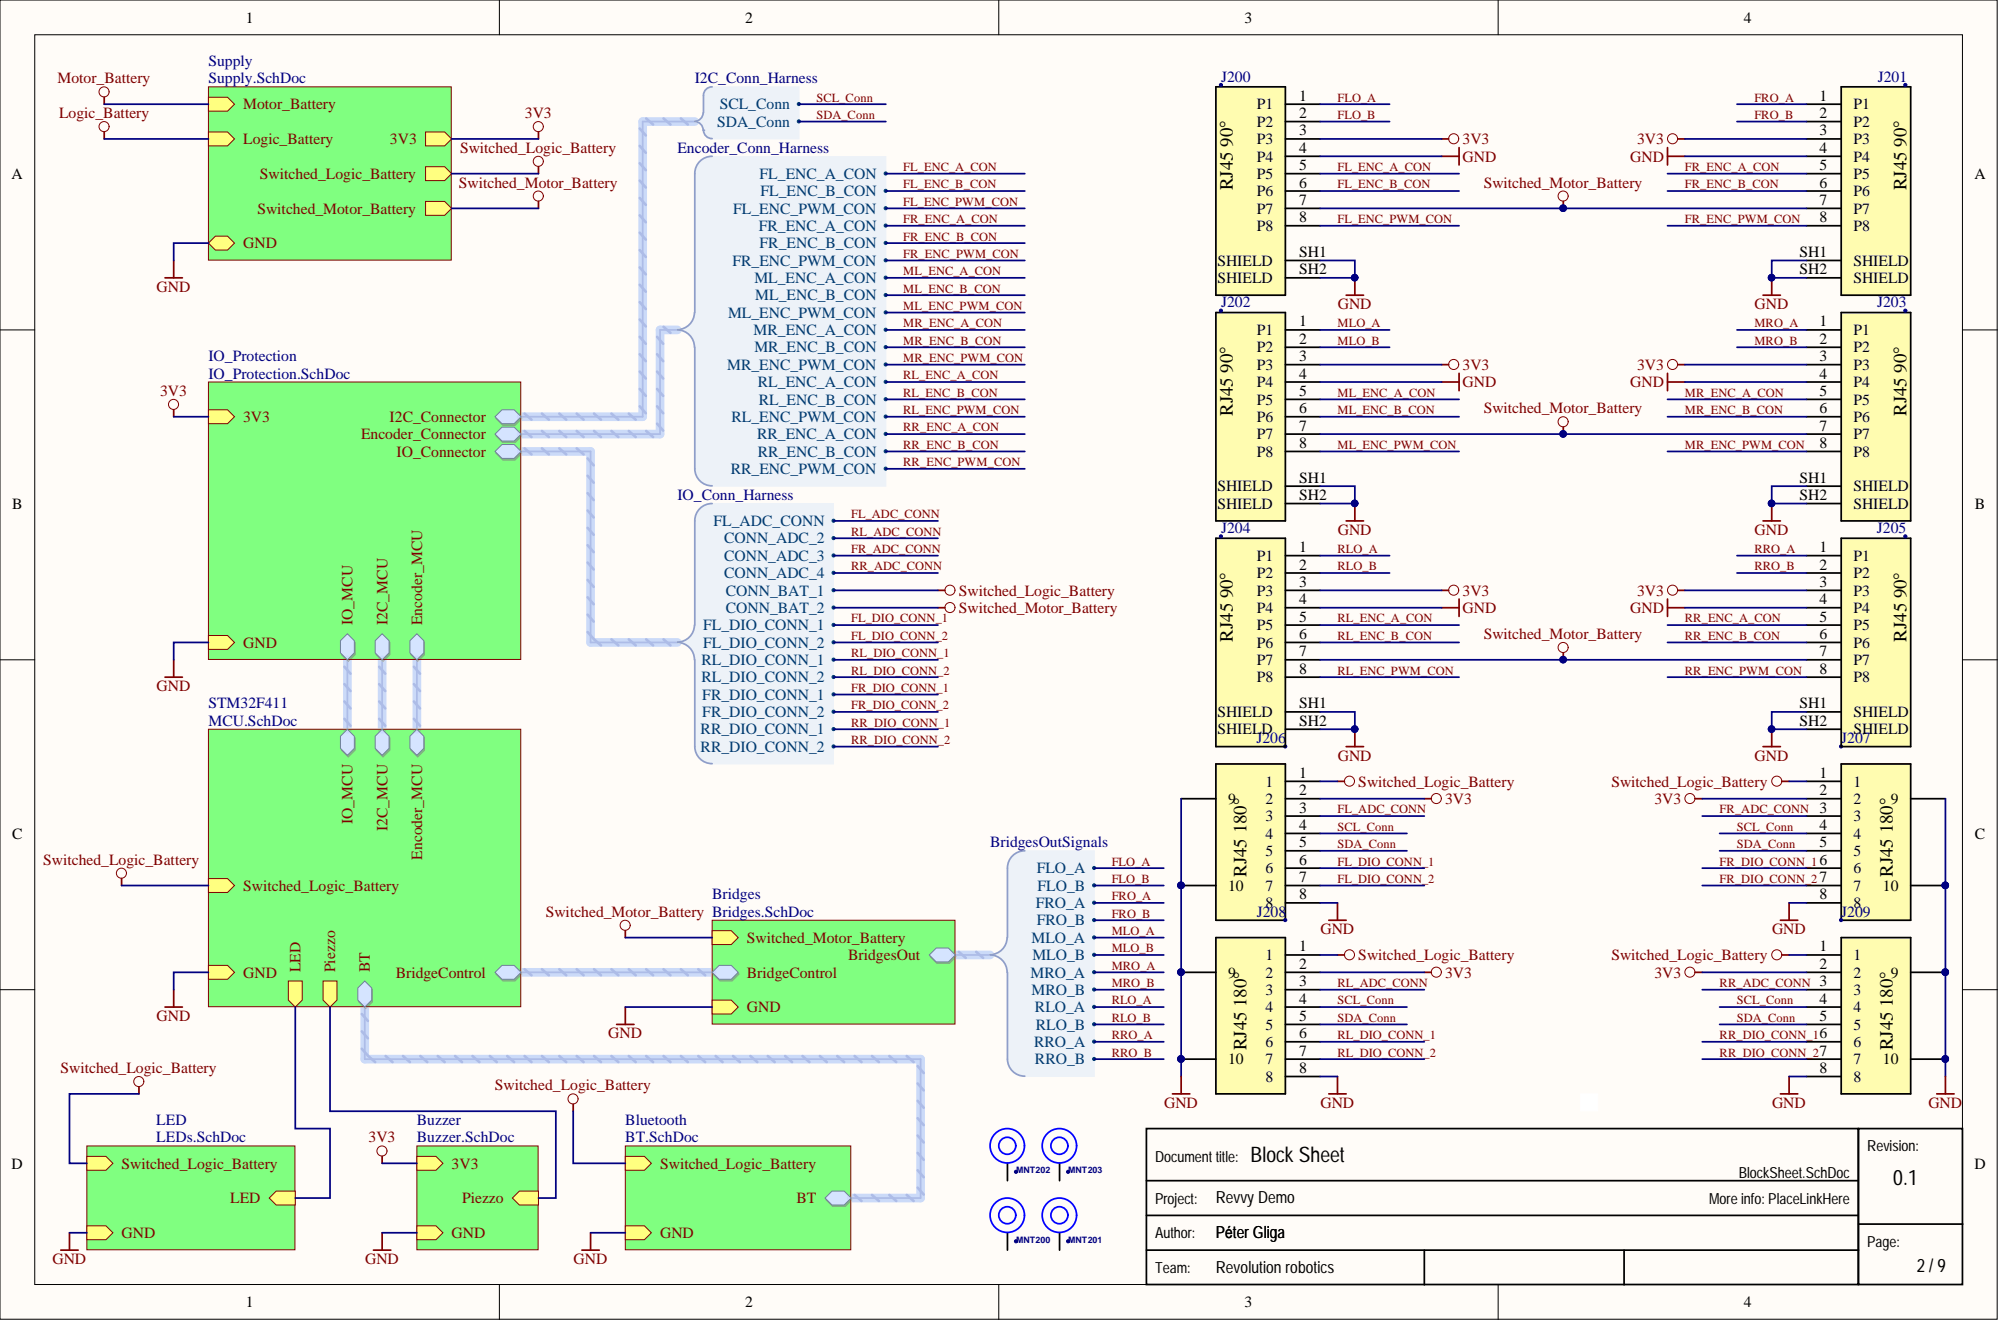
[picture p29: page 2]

GND

Team: Revolution robotics

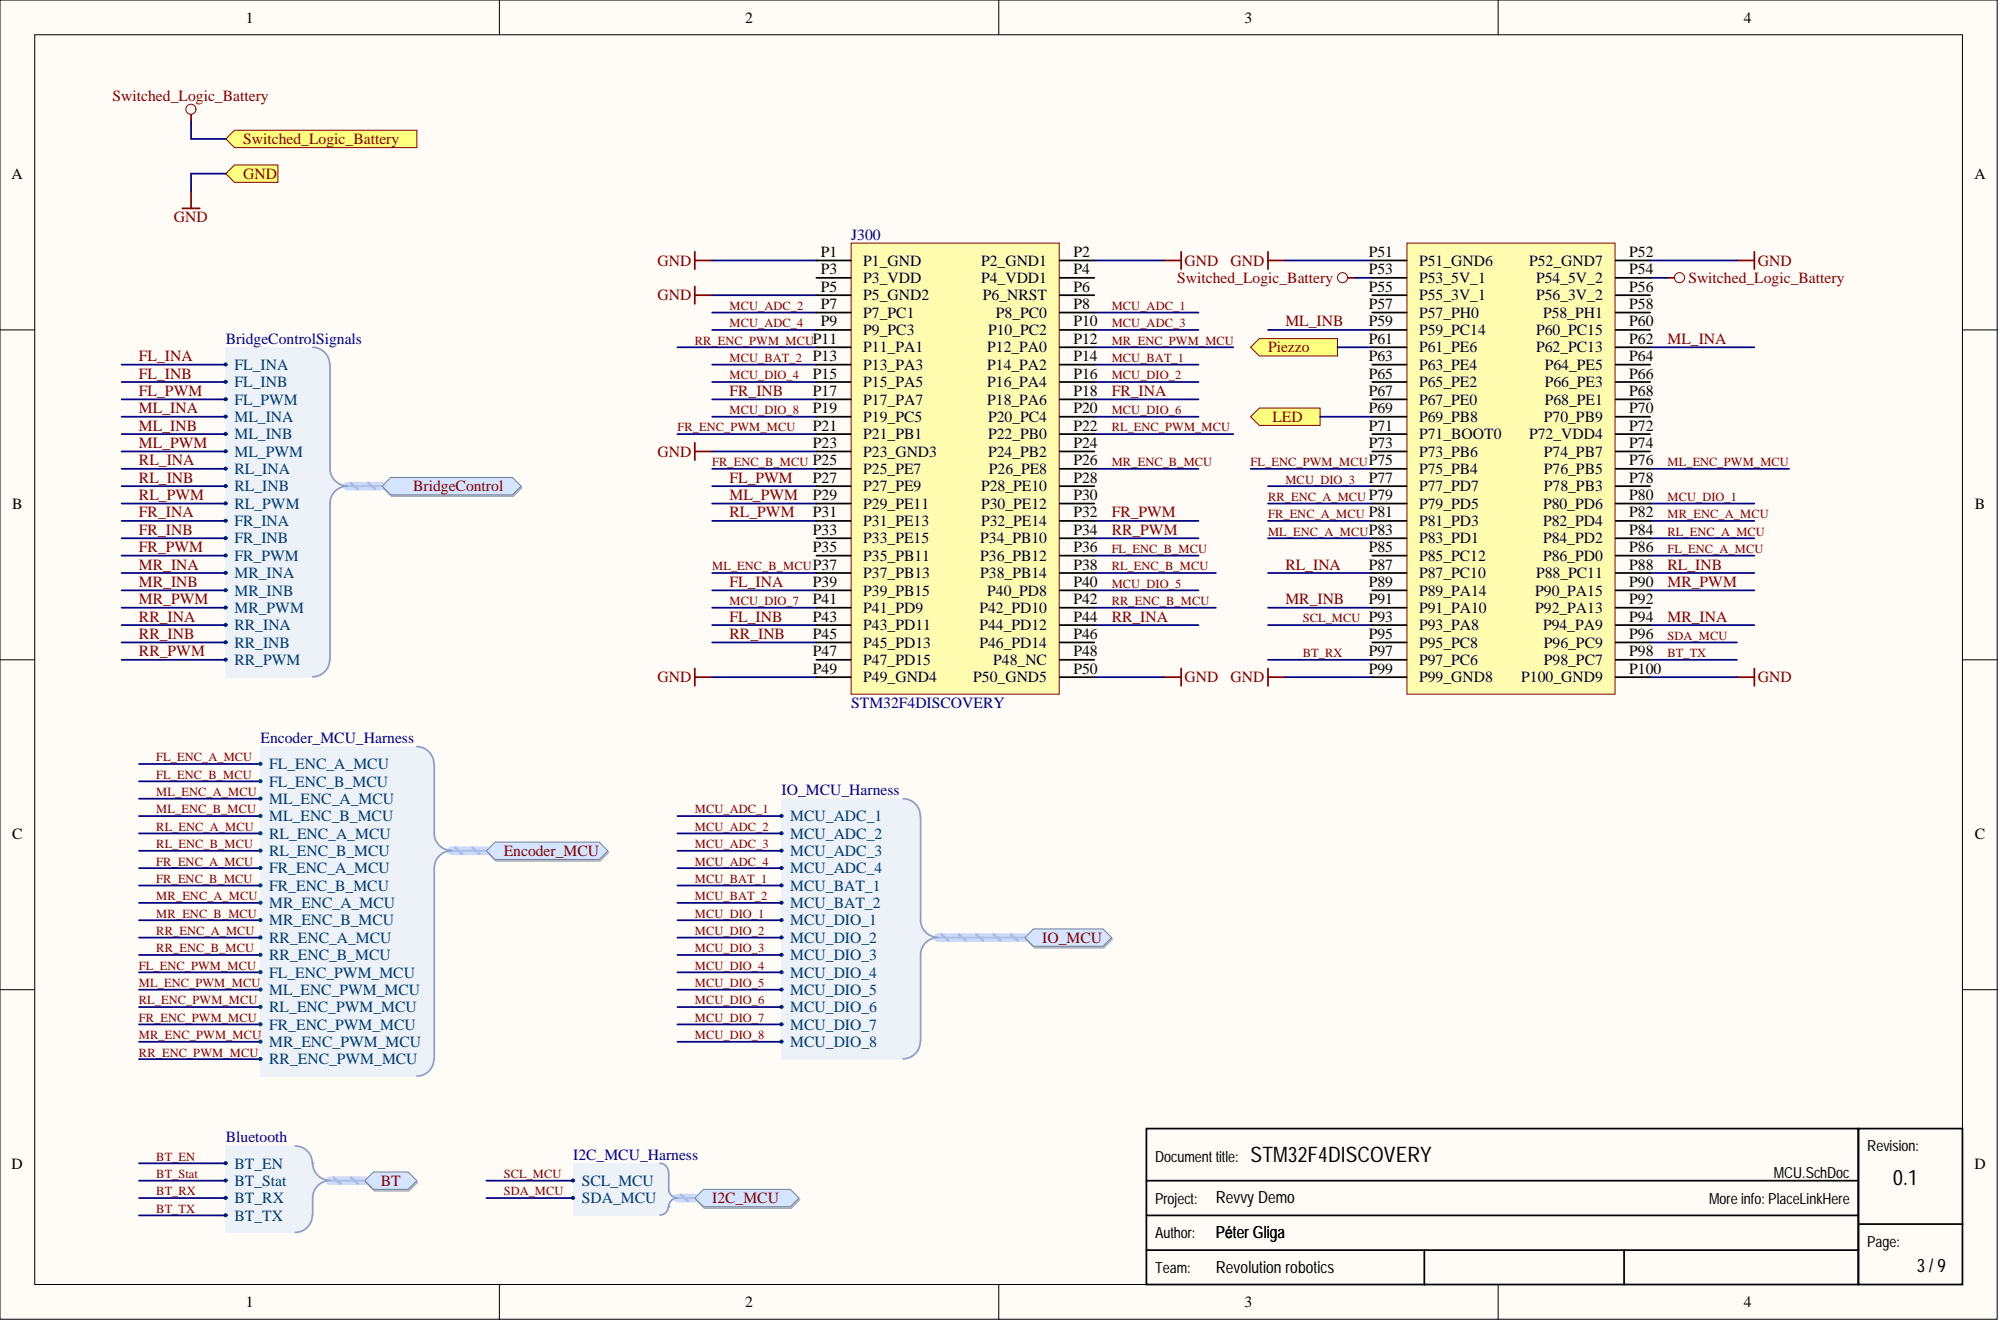
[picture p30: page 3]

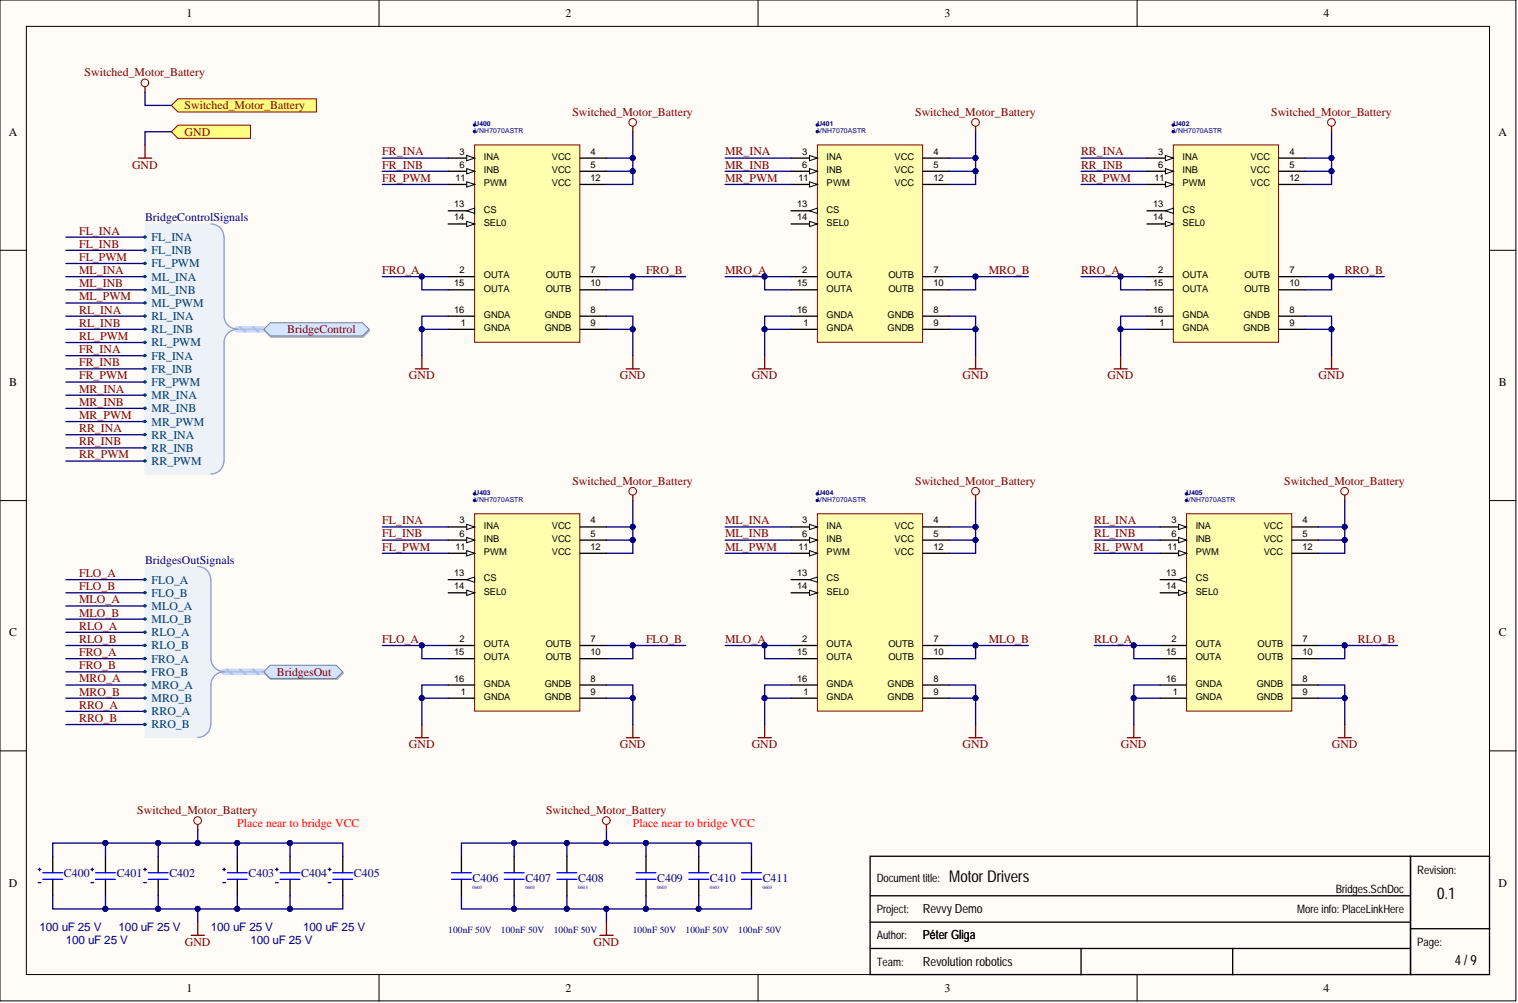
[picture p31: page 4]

Place near to bridge VCC

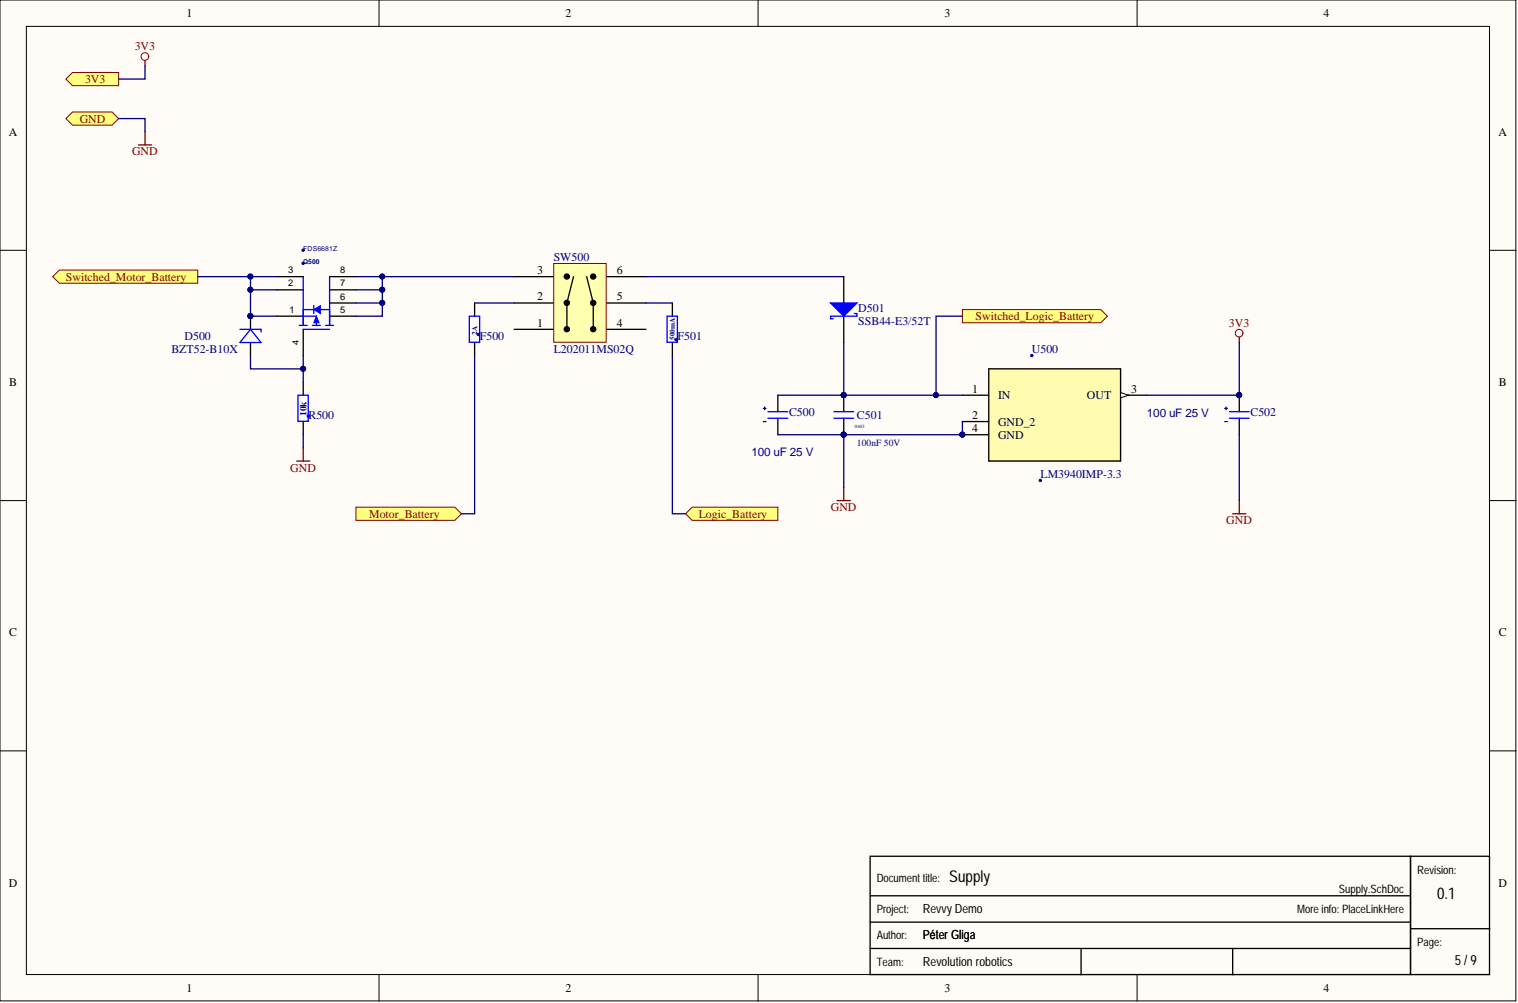
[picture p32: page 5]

C501 | GND 4 GND_2 2


Place near to LED





hotfix:
Remove R42 and R48 from STM Disco
Remove U7 (MEMS GYRO)
Led supply cannot be higher than 5V

In next revision:
re allocate PC0 PD5 PA9
re allocate PA6
ADD 7805 for logic battery (also for led supply)
add footprint for 6pin ws2812

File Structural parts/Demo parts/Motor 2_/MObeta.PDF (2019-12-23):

RJ45 socket without LEDs; Magnet disc; FINISH:; DEBURR AND; BREAK SHARP; DO NOT SCALE DRAWING; REVISION; SCALE:1:1; SHEET 1 OF 3

Two rotating hubs (#MOhA) are connected
to the gearbox's output
Two hubs are rotating together

Gearbox with 64:1 ratio

RJ45 socket can protrude as much
as necessary

Interface PCB to connect RJ45 to
hall encoder and motor

The square shaped
hole should enable
user to push a
square shaped axle
through the whole motor

UNLESS OTHERWISE SPECIFIED:
DIMENSIONS ARE IN MILLIMETERS
SURFACE FINISH:
TOLERANCES:
LINEAR:
ANGULAR:

NAME | SIGNATURE | DATE | | | | TITLE:

DRAWN
CHK'D
APPV'D
MFG
Q.A | | | | MATERIAL: | DWG NO. MOcA Exploded view | A3

28,00 min 10,00; min 5,00; wheel size; SECTION B-B; SCALE 2 : 1; DETAIL C; FINISH:; DEBURR AND; BREAK SHARP; DO NOT SCALE DRAWING; REVISION

RJ45 socket can protrude as much
as needed

This holes are mandatory
on both top and bottom sides!

UNLESS OTHERWISE SPECIFIED:
DIMENSIONS ARE IN MILLIMETERS
SURFACE FINISH:
TOLERANCES:
LINEAR:
ANGULAR:

0,65 is the nominal value,
it can be in the range
but >0,8mm and <0,5 is
strictly prohibited

NAME | SIGNATURE | DATE | | | TITLE:

DRAWN
CHK'D
APPV'D
MFG

MOcA + MOhA

SCALE:1:1 | SHEET 2 OF 3

SECTION E-E; SECTION F-F; SECTION G-G; FINISH:; DEBURR AND; BREAK SHARP; DO NOT SCALE DRAWING; REVISION

UNLESS OTHERWISE SPECIFIED:
DIMENSIONS ARE IN MILLIMETERS
SURFACE FINISH:
TOLERANCES:
LINEAR:
ANGULAR:

NAME | SIGNATURE | DATE | | | TITLE:

DRAWN
CHK'D
APPV'D
MFG

MOhA

SCALE:2:1 | SHEET 3 OF 3

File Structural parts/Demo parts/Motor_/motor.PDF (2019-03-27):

RJ45 socket without LEDs; Magnet disc; FINISH:; DEBURR AND; BREAK SHARP; DO NOT SCALE DRAWING; REVISION; SCALE:1:1; SHEET 1 OF 3

Two rotating hubs (#MOhA) are connected
to the gearbox's output
Two hubs are rotating together

Gearbox with 64:1 ratio

RJ45 socket can protrude as much
as necessary

Interface PCB to connect RJ45 to
hall encoder and motor

The square shaped
hole should enable
user to push a
square shaped axle
through the whole motor

UNLESS OTHERWISE SPECIFIED:
DIMENSIONS ARE IN MILLIMETERS
SURFACE FINISH:
TOLERANCES:
LINEAR:
ANGULAR:

NAME | SIGNATURE | DATE | | | | TITLE:

DRAWN
CHK'D
APPV'D
MFG
Q.A | | | | MATERIAL: | DWG NO. MOcA Exploded view | A3

min 10.00; min 5,00; SECTION B-B; SCALE 2 : 1; 0,80 is the nominal value,; DETAIL C; FINISH:; DEBURR AND; BREAK SHARP; DO NOT SCALE DRAWING; REVISION

RJ45 socket can protrude as much
as needed

This holes are mandatory
on both top and bottom sides!

it can be in the range
but >0,80mm is strictly prohibited

UNLESS OTHERWISE SPECIFIED:
DIMENSIONS ARE IN MILLIMETERS
SURFACE FINISH:
TOLERANCES:
LINEAR:
ANGULAR:

NAME | SIGNATURE | DATE | | | TITLE:

DRAWN
CHK'D
APPV'D
MFG

MOcA + MOhA

SCALE:1:1 | SHEET 2 OF 3

SECTION E-E; SECTION F-F; SECTION G-G; FINISH:; DEBURR AND; BREAK SHARP; DO NOT SCALE DRAWING; REVISION

UNLESS OTHERWISE SPECIFIED:
DIMENSIONS ARE IN MILLIMETERS
SURFACE FINISH:
TOLERANCES:
LINEAR:
ANGULAR:

NAME | SIGNATURE | DATE | | | TITLE:

DRAWN
CHK'D
APPV'D
MFG

MOhA

SCALE:2:1 | SHEET 3 OF 3

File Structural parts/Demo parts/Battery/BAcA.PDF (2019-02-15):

Top view; Bottom view; SECTION A-A; FINISH:; DEBURR AND; BREAK SHARP; DO NOT SCALE DRAWING; REVISION; SCALE:1:1; SHEET 1 OF 2

6xAA rechargable batteries
inside a quick swap holder

Snap fit door

recessed area for labelling

UNLESS OTHERWISE SPECIFIED:
DIMENSIONS ARE IN MILLIMETERS
SURFACE FINISH:
TOLERANCES:
LINEAR:
ANGULAR:

NAME | SIGNATURE | DATE | | | | TITLE:

DRAWN
CHK'D
APPV'D
MFG
Q.A | | | | MATERIAL: | DWG NO. BAcA | A3

the snap connector than on the picture on the right A; FINISH:; DEBURR AND; BREAK SHARP; DO NOT SCALE DRAWING; REVISION; SCALE:1:2; SHEET 2 OF 2

DC plug male comes from
the battery case top face with a cable

Snap fit door

DC plug female on brain

4xMOcA
below brain and battery

6xAA batteries
in a quick swap holder
to replace all batteries at the same time
Batteries can be replaced in the quick swap holder

This face has a recessed area for labeling
and connects to the brain case
as pictured above right

UNLESS OTHERWISE SPECIFIED:
DIMENSIONS ARE IN MILLIMETERS
SURFACE FINISH:
TOLERANCES:
LINEAR:
ANGULAR:

NAME | SIGNATURE | DATE | | | | TITLE:

Quick swap electrical connection of battery holder
to be designed by CM.
Preferably a better connection for

DRAWN
CHK'D
APPV'D
MFG
Q.A | | | | MATERIAL: | DWG NO. BAcA | A3





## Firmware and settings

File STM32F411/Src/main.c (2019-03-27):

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

/* Includes ------------------------------------------------------------------*/
#include "main.h"
#include "cmsis_os.h"

/* USER CODE BEGIN Includes */
#include <math.h>
#include <stdlib.h>
#include "WS2812_Lib.h"
#include "stm32f411e_discovery.h"
#include "stm32f411e_discovery_accelerometer.h"
/* USER CODE END Includes */

ADC_HandleTypeDef hadc1;
DMA_HandleTypeDef hdma_adc1;

CRC_HandleTypeDef hcrc;

I2C_HandleTypeDef hi2c1;
I2C_HandleTypeDef hi2c3;

SPI_HandleTypeDef hspi5;
DMA_HandleTypeDef hdma_spi5_tx;

TIM_HandleTypeDef htim1;
TIM_HandleTypeDef htim2;
TIM_HandleTypeDef htim3;
TIM_HandleTypeDef htim4;
TIM_HandleTypeDef htim5;
TIM_HandleTypeDef htim9;
TIM_HandleTypeDef htim10;
DMA_HandleTypeDef hdma_tim4_ch2;

UART_HandleTypeDef huart6;

osThreadId defaultTaskHandle;
osThreadId sensorTaskHandle;
osThreadId controlTaskHandle;
osThreadId commTaskHandle;
osThreadId idleTaskHandle;
osThreadId ledTaskHandle;
osThreadId applicationTaskHandle;
/* USER CODE BEGIN PV */
#define ABS(x)         (x < 0) ? (-x) : x
#define PI     3.14159

#define COMPASS_X_MAX 702
#define COMPASS_X_MIN -358
#define COMPASS_Y_MAX 293
#define COMPASS_Y_MIN -829
#define COMPASS_Z_MAX 845
#define COMPASS_Z_MIN -282

#define NORMALVOLTAGE_MOT 1.4
#define LOWVOLTAGE_MOT 1.18

#define NORMALVOLTAGE_LOGIC 1.1
#define LOWVOLTAGE_LOGIC 0.8

static volatile uint32_t ADC_Buf[6];
static volatile uint32_t ADC_Values[6];

static uint16_t mot1Cntr, mot1CntrPrev = 0; //L1
static uint16_t mot2Cntr, mot2CntrPrev = 0; //L2
static uint16_t mot3Cntr, mot3CntrPrev = 0; //L3
static uint16_t mot4Cntr, mot4CntrPrev = 0; //R1
static uint16_t mot5Cntr, mot5CntrPrev = 0; //R2
static uint16_t mot6Cntr, mot6CntrPrev = 0; //R3
static volatile uint8_t mot1Dir = 0; //L1
static volatile uint8_t mot2Dir = 0; //L2
static volatile uint8_t mot3Dir = 0; //L3
static volatile uint8_t mot4Dir = 0; //R1
static volatile uint8_t mot5Dir = 0; //R2
static volatile uint8_t mot6Dir = 0; //R3

static volatile uint32_t sen1Cntr, sen1Start, sen1End, sen1Length = 0; //Sensors
static volatile uint32_t sen2Cntr, sen2Start, sen2End, sen2Length = 0; //Sensors
static volatile uint32_t sen3Cntr, sen3Start, sen3End, sen3Length = 0; //Sensors
static volatile uint32_t sen4Cntr, sen4Start, sen4End, sen4Length = 0; //Sensors
static volatile float sen1Distance, sen1DistanceFiltered, sen1DistancePrev = 0;
static volatile float sen2Distance, sen2DistanceFiltered, sen2DistancePrev = 0;
static volatile float sen3Distance, sen3DistanceFiltered, sen3DistancePrev = 0;
static volatile float sen4Distance, sen4DistanceFiltered, sen4DistancePrev = 0;

static volatile uint16_t sen1DebounceCounter = 1000;
static volatile uint16_t sen2DebounceCounter = 1000;
static volatile uint16_t sen3DebounceCounter = 1000;
static volatile uint16_t sen4DebounceCounter = 1000;

static volatile float batteryVoltage1 = 0;
static volatile float batteryVoltage2 = 0;

static volatile uint16_t sen1AnalogValue = 0;
static volatile uint16_t sen2AnalogValue = 0;
static volatile uint16_t sen3AnalogValue = 0;
static volatile uint16_t sen4AnalogValue = 0;

static volatile uint32_t internalCounter = 0;

static volatile float roll,pitch,heading = 0;
static volatile float fNormAcc,fSinRoll,fCosRoll,fSinPitch,fCosPitch = 0.0f;
static volatile float accX,accY,accZ = 0;
static volatile float accXFiltered,accYFiltered,accZFiltered = 0;
static volatile float compassX,compassY,compassZ = 0;

static volatile float wheelL1Odometer_m, wheelL1Odometer_m_prev = 0;
static volatile float wheelL2Odometer_m, wheelL2Odometer_m_prev = 0;
static volatile float wheelL3Odometer_m, wheelL3Odometer_m_prev = 0;
static volatile float wheelR1Odometer_m, wheelR1Odometer_m_prev = 0;
static volatile float wheelR2Odometer_m, wheelR2Odometer_m_prev = 0;
static volatile float wheelR3Odometer_m, wheelR3Odometer_m_prev = 0;
static volatile float wheelL1Angle_deg = 0;
static volatile float wheelL2Angle_deg = 0;
static volatile float wheelL3Angle_deg = 0;
static volatile float wheelR1Angle_deg = 0;
static volatile float wheelR2Angle_deg = 0;
static volatile float wheelR3Angle_deg = 0;

static volatile float wheelL1RawVelocity_mps, wheelL1FiltVelocity_mps, wheelL1FiltVelocity_rpm = 0;
static volatile float wheelL2RawVelocity_mps, wheelL2FiltVelocity_mps, wheelL2FiltVelocity_rpm = 0;
static volatile float wheelL3RawVelocity_mps, wheelL3FiltVelocity_mps, wheelL3FiltVelocity_rpm = 0;
static volatile float wheelR1RawVelocity_mps, wheelR1FiltVelocity_mps, wheelR1FiltVelocity_rpm = 0;
static volatile float wheelR2RawVelocity_mps, wheelR2FiltVelocity_mps, wheelR2FiltVelocity_rpm = 0;
static volatile float wheelR3RawVelocity_mps, wheelR3FiltVelocity_mps, wheelR3FiltVelocity_rpm = 0;

static volatile float wheelSize_m = 0.20; // 20cm circumference
//static volatile uint16_t encoderSignalsPerRound = 360; // 3 counts per motor round and a 120:1 gearbox
static volatile uint16_t encoderSignalsPerRound = 144; // 3 counts per motor round and a 48:1 gearbox
static volatile uint16_t speedSensingTaskCycle_ms = 10; // 10ms task cycle time
//static volatile float maxVelocity = 0.15; // for the 120:1 gears!
static volatile float maxVelocity = 0.5; // for the 48:1 gears!

static volatile float referenceSpeedLeft = 0;
static volatile float referenceSpeedRight = 0;

static volatile uint32_t timeStamp =0;
static volatile uint32_t timeOutGuard, timeOutGuardMax =0;
static uint8_t receiveBuffer[10]={0};
static volatile float referenceSpeed = 0;
static volatile float referenceAngle = 0;
static uint8_t messageCounter, messageCounterPrev = 0;
static volatile uint8_t buttonState = 0;

static volatile float nextSpeedLeft, nextSpeedRight = 0;
static volatile float reqSpeedLeft, reqSpeedRight, currSpeedLeft, currSpeedRight = 0;
static volatile float speedRampRate = 0.05;

static volatile float wheelL1VelocityError, wheelL1VelocityErrorBefore, wheelL1VelocityIntError, wheelL1VelocityDerivatedError, wheelL1SumControl, wheelL1SumControlBeforeSaturation = 0;
static volatile float wheelL2VelocityError, wheelL2VelocityErrorBefore, wheelL2VelocityIntError, wheelL2VelocityDerivatedError, wheelL2SumControl, wheelL2SumControlBeforeSaturation = 0;
static volatile float wheelL3VelocityError, wheelL3VelocityErrorBefore, wheelL3VelocityIntError, wheelL3VelocityDerivatedError, wheelL3SumControl, wheelL3SumControlBeforeSaturation = 0;
static volatile float wheelR1VelocityError, wheelR1VelocityErrorBefore, wheelR1VelocityIntError, wheelR1VelocityDerivatedError, wheelR1SumControl, wheelR1SumControlBeforeSaturation = 0;
static volatile float wheelR2VelocityError, wheelR2VelocityErrorBefore, wheelR2VelocityIntError, wheelR2VelocityDerivatedError, wheelR2SumControl, wheelR2SumControlBeforeSaturation = 0;
static volatile float wheelR3VelocityError, wheelR3VelocityErrorBefore, wheelR3VelocityIntError, wheelR3VelocityDerivatedError, wheelR3SumControl, wheelR3SumControlBeforeSaturation = 0;

static volatile float maxDutyCycle = 100;
static volatile float antiWindup = 0.01;//0.004;
static volatile float ctrlP = 400;//750;
static volatile float ctrlI = 8;//10;
static volatile float ctrlD = 2;

static volatile float positionErrorL3_deg = 0;
static volatile float referenceAngleL3_deg = 0;
static volatile float positionErrorR3_deg = 0;
static volatile float referenceAngleR3_deg = 0;
static volatile float ctrlP_pos = 0.004;
static volatile float angleIncrement = 0.5;

static volatile uint16_t ultrasonicDebounceLimit = 50;
static volatile uint8_t ultrasonicActive = 0;
static volatile uint8_t bumperActive = 0;
static volatile uint8_t autonomousActive = 0;
/* USER CODE END PV */

void SystemClock_Config(void);
static void MX_GPIO_Init(void);
static void MX_DMA_Init(void);
static void MX_TIM1_Init(void);
static void MX_TIM2_Init(void);
static void MX_I2C1_Init(void);
static void MX_ADC1_Init(void);
static void MX_CRC_Init(void);
static void MX_USART6_UART_Init(void);
static void MX_TIM3_Init(void);
static void MX_TIM4_Init(void);
static void MX_TIM5_Init(void);
static void MX_I2C3_Init(void);
static void MX_TIM9_Init(void);
static void MX_TIM10_Init(void);
static void MX_SPI5_Init(void);
void StartDefaultTask(void const * argument);
void StartSensorTask(void const * argument);
void StartControlTask(void const * argument);
void StartCommTask(void const * argument);
void StartIdleTask(void const * argument);
void StartLedTask(void const * argument);
void StartApplicationTask(void const * argument);

/* USER CODE BEGIN PFP */

/* USER CODE END PFP */

/* USER CODE BEGIN 0 */
void HAL_ADC_ConvCpltCallback(ADC_HandleTypeDef* hadc){
  
  if(hadc->Instance==ADC1){
    ADC_Values[0] = ADC_Buf[0];
    ADC_Values[1] = ADC_Buf[1];
    ADC_Values[2] = ADC_Buf[2];
    ADC_Values[3] = ADC_Buf[3];
    ADC_Values[4] = ADC_Buf[4];
    ADC_Values[5] = ADC_Buf[5];
  }
}
/* USER CODE END 0 */

/**
  * @brief  The application entry point.
  * @retval int
  */
int main(void)
{
  /* MCU Configuration--------------------------------------------------------*/

  /* Reset of all peripherals, Initializes the Flash interface and the Systick. */
  HAL_Init();

  /* Configure the system clock */
  SystemClock_Config();

  /* Initialize all configured peripherals */
  MX_GPIO_Init();
  MX_DMA_Init();
  MX_TIM1_Init();
  MX_TIM2_Init();
  MX_I2C1_Init();
  MX_ADC1_Init();
  MX_CRC_Init();
  MX_USART6_UART_Init();
  MX_TIM3_Init();
  MX_TIM4_Init();
  MX_TIM5_Init();
  MX_I2C3_Init();
  MX_TIM9_Init();
  MX_TIM10_Init();
  MX_SPI5_Init();
  /* USER CODE BEGIN 2 */
  
  // 6*PWM signals for the 6 DC motors
  HAL_TIM_PWM_Start(&htim1, TIM_CHANNEL_1);
  HAL_TIMEx_PWMN_Start(&htim1, TIM_CHANNEL_1);
  HAL_TIM_PWM_Start(&htim1, TIM_CHANNEL_2);
  HAL_TIMEx_PWMN_Start(&htim1, TIM_CHANNEL_2);
  HAL_TIM_PWM_Start(&htim1, TIM_CHANNEL_3);
  HAL_TIMEx_PWMN_Start(&htim1, TIM_CHANNEL_3);
  HAL_TIM_PWM_Start(&htim1, TIM_CHANNEL_4);
  HAL_TIMEx_PWMN_Start(&htim1, TIM_CHANNEL_4);
  HAL_TIM_PWM_Start(&htim2, TIM_CHANNEL_1);
  HAL_TIMEx_PWMN_Start(&htim2, TIM_CHANNEL_1);
  HAL_TIM_PWM_Start(&htim2, TIM_CHANNEL_3);
  HAL_TIMEx_PWMN_Start(&htim2, TIM_CHANNEL_3);
  // 6*PWM signals for the 6 servos
  HAL_TIM_PWM_Start(&htim3, TIM_CHANNEL_1);
  HAL_TIMEx_PWMN_Start(&htim3, TIM_CHANNEL_1);
  HAL_TIM_PWM_Start(&htim3, TIM_CHANNEL_2);
  HAL_TIMEx_PWMN_Start(&htim3, TIM_CHANNEL_2);
  HAL_TIM_PWM_Start(&htim3, TIM_CHANNEL_3);
  HAL_TIMEx_PWMN_Start(&htim3, TIM_CHANNEL_3);
  HAL_TIM_PWM_Start(&htim3, TIM_CHANNEL_4);
  HAL_TIMEx_PWMN_Start(&htim3, TIM_CHANNEL_4);
  HAL_TIM_PWM_Start(&htim5, TIM_CHANNEL_1);
  HAL_TIMEx_PWMN_Start(&htim5, TIM_CHANNEL_1);
  HAL_TIM_PWM_Start(&htim5, TIM_CHANNEL_2);
  HAL_TIMEx_PWMN_Start(&htim5, TIM_CHANNEL_2);
  // 1*PWM signal for buzzer
  HAL_TIM_PWM_Start(&htim9, TIM_CHANNEL_2);
  HAL_TIMEx_PWMN_Start(&htim9, TIM_CHANNEL_2);
  
  //Start internal timer for 10us time measurement
  HAL_TIM_Base_Start(&htim10);
  
  // Test code START
  TIM1->CCR1 = 00*4800/100; //LEFT1
  TIM1->CCR2 = 00*4800/100; //LEFT2
  TIM1->CCR3 = 00*4800/100; //LEFT3
  TIM1->CCR4 = 00*4800/100; //RIGHT1
  TIM2->CCR1 = 00*4800/100; //RIGHT2
  TIM2->CCR3 = 00*4800/100; //RIGHT3
 
  TIM3->CCR1 = 5*20000/100; //SERVO1 - L1
  TIM3->CCR2 = 5*20000/100; //SERVO2 - L2
  TIM3->CCR3 = 5*20000/100; //SERVO3 - L3
  TIM3->CCR4 = 5*20000/100; //SERVO4 - L4
  TIM5->CCR1 = 5*20000/100; //SERVO5 - L5
  TIM5->CCR2 = 5*20000/100; //SERVO6 - L6
  
  TIM9->CCR2 = 0*2400/100; //Buzzer
  
  HAL_GPIO_WritePin(GPIOB, GPIO_PIN_15, GPIO_PIN_RESET); //LEFT1 FW
  HAL_GPIO_WritePin(GPIOD, GPIO_PIN_11, GPIO_PIN_SET); //LEFT1 RW
  HAL_GPIO_WritePin(GPIOC, GPIO_PIN_13, GPIO_PIN_RESET); //LEFT2 FW
  HAL_GPIO_WritePin(GPIOC, GPIO_PIN_14, GPIO_PIN_SET); //LEFT2 RW
  HAL_GPIO_WritePin(GPIOC, GPIO_PIN_10, GPIO_PIN_RESET); //LEFT3 FW
  HAL_GPIO_WritePin(GPIOC, GPIO_PIN_11, GPIO_PIN_SET); //LEFT3 RW
  HAL_GPIO_WritePin(GPIOA, GPIO_PIN_6,  GPIO_PIN_RESET); //RIGHT1 FW
  HAL_GPIO_WritePin(GPIOA, GPIO_PIN_7,  GPIO_PIN_SET); //RIGHT1 RW
  HAL_GPIO_WritePin(GPIOA, GPIO_PIN_9,  GPIO_PIN_RESET); //RIGHT2 FW
  HAL_GPIO_WritePin(GPIOA, GPIO_PIN_10, GPIO_PIN_SET); //RIGHT2 RW
  HAL_GPIO_WritePin(GPIOD, GPIO_PIN_12, GPIO_PIN_RESET); //RIGHT3 FW
  HAL_GPIO_WritePin(GPIOD, GPIO_PIN_13, GPIO_PIN_SET); //RIGHT3 RW
  HAL_GPIO_WritePin(GPIOA, GPIO_PIN_4,  GPIO_PIN_RESET); //SEN1 OUT
  HAL_GPIO_WritePin(GPIOA, GPIO_PIN_5,  GPIO_PIN_RESET); //SEN2 OUT
  HAL_GPIO_WritePin(GPIOC, GPIO_PIN_4,  GPIO_PIN_RESET); //SEN3 OUT
  HAL_GPIO_WritePin(GPIOC, GPIO_PIN_5,  GPIO_PIN_RESET); //SEN4 OUT
  // Test code END
  
  BSP_ACCELERO_Init();
  MAGNET_Init();
  
  /* USER CODE END 2 */

  /* USER CODE BEGIN RTOS_MUTEX */
  /* add mutexes, ... */
  /* USER CODE END RTOS_MUTEX */

  /* USER CODE BEGIN RTOS_SEMAPHORES */
  /* add semaphores, ... */
  /* USER CODE END RTOS_SEMAPHORES */

  /* USER CODE BEGIN RTOS_TIMERS */
  /* start timers, add new ones, ... */
  /* USER CODE END RTOS_TIMERS */

  /* Create the thread(s) */
  /* definition and creation of defaultTask */
  osThreadDef(defaultTask, StartDefaultTask, osPriorityIdle, 0, 128);
  defaultTaskHandle = osThreadCreate(osThread(defaultTask), NULL);

  /* definition and creation of sensorTask */
  osThreadDef(sensorTask, StartSensorTask, osPriorityNormal, 0, 128);
  sensorTaskHandle = osThreadCreate(osThread(sensorTask), NULL);

  /* definition and creation of controlTask */
  osThreadDef(controlTask, StartControlTask, osPriorityHigh, 0, 128);
  controlTaskHandle = osThreadCreate(osThread(controlTask), NULL);

  /* definition and creation of commTask */
  osThreadDef(commTask, StartCommTask, osPriorityAboveNormal, 0, 128);
  commTaskHandle = osThreadCreate(osThread(commTask), NULL);

  /* definition and creation of idleTask */
  osThreadDef(idleTask, StartIdleTask, osPriorityLow, 0, 128);
  idleTaskHandle = osThreadCreate(osThread(idleTask), NULL);

  /* definition and creation of ledTask */
  osThreadDef(ledTask, StartLedTask, osPriorityNormal, 0, 128);
  ledTaskHandle = osThreadCreate(osThread(ledTask), NULL);

  /* definition and creation of applicationTask */
  osThreadDef(applicationTask, StartApplicationTask, osPriorityNormal, 0, 128);
  applicationTaskHandle = osThreadCreate(osThread(applicationTask), NULL);

  /* USER CODE BEGIN RTOS_THREADS */
  /* add threads, ... */
  /* USER CODE END RTOS_THREADS */

  /* USER CODE BEGIN RTOS_QUEUES */
  /* add queues, ... */
  /* USER CODE END RTOS_QUEUES */
 

  /* Start scheduler */
  osKernelStart();
  
  /* We should never get here as control is now taken by the scheduler */

  /* Infinite loop */
  /* USER CODE BEGIN WHILE */
  while (1)
  {

    /* USER CODE END WHILE */

    /* USER CODE BEGIN 3 */

  }
  /* USER CODE END 3 */
}

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
/* USER CODE BEGIN 4 */
void HAL_GPIO_EXTI_Callback(uint16_t GPIO_Pin){
  switch ( GPIO_Pin ) {
  case GPIO_PIN_0:
    if (HAL_GPIO_ReadPin(GPIOB, GPIO_PIN_12)) mot1Cntr++;
    else mot1Cntr--;
    break;
  case GPIO_PIN_1:
    if (HAL_GPIO_ReadPin(GPIOB, GPIO_PIN_13)) mot2Cntr++;
    else mot2Cntr--;
    break;
  case GPIO_PIN_2:
    if (HAL_GPIO_ReadPin(GPIOB, GPIO_PIN_14)) mot3Cntr++;
    else mot3Cntr--;
    break;
  case GPIO_PIN_3:
    if (HAL_GPIO_ReadPin(GPIOE, GPIO_PIN_7)) mot4Cntr++;
    else mot4Cntr--;
    break;
  case GPIO_PIN_4:
    if (HAL_GPIO_ReadPin(GPIOE, GPIO_PIN_8)) mot5Cntr++;
    else mot5Cntr--;
    break;
  case GPIO_PIN_5:
    if (HAL_GPIO_ReadPin(GPIOD, GPIO_PIN_10)) mot6Cntr++;
    else mot6Cntr--;
    break;
  case GPIO_PIN_6:
    sen1Cntr++;
    if (HAL_GPIO_ReadPin(GPIOD, GPIO_PIN_6)) sen1Start = TIM10->CNT;
    else {
      sen1End = TIM10->CNT;
      if (sen1End > sen1Start) sen1Length = sen1End-sen1Start;
      else sen1Length = (sen1End+65535)-sen1Start;
    }
    break; 
  case GPIO_PIN_7:
    sen2Cntr++;
    if (HAL_GPIO_ReadPin(GPIOD, GPIO_PIN_7)) sen2Start = TIM10->CNT;
    else {
      sen2End = TIM10->CNT;
      if (sen2End > sen2Start) sen2Length = sen2End-sen2Start;
      else sen2Length = (sen2End+65535)-sen2Start;
    }
    break; 
  case GPIO_PIN_8:
    sen3Cntr++;
    if (HAL_GPIO_ReadPin(GPIOD, GPIO_PIN_8)) sen3Start = TIM10->CNT;
    else {
      sen3End = TIM10->CNT;
      if (sen3End > sen3Start) sen3Length = sen3End-sen3Start;
      else sen3Length = (sen3End+65535)-sen3Start;
    }
    break; 
  case GPIO_PIN_9:
    sen4Cntr++;
    if (HAL_GPIO_ReadPin(GPIOD, GPIO_PIN_9)) sen4Start = TIM10->CNT;
    else {
      sen4End = TIM10->CNT;
      if (sen4End > sen4Start) sen4Length = sen4End-sen4Start;
      else sen4Length = (sen4End+65535)-sen4Start;
    }
    break; 
  default:
    break;
  }
}

float filter2 (float avg, float input, float alpha) {
  avg = (alpha * input) + (1.0 - alpha) * avg;
  return avg;
}

void saturateInteger(int16_t* i, int16_t min, int16_t max) {
  int16_t val = *i;
  if (val < min) val = min;
  else if (val > max) val = max;
  *i = val;
}

void saturateVolatileFloat(volatile float* i, float min, float max) {
  float val = *i;
  if (val < min) val = min;
  else if (val > max) val = max;
  *i = val;
}

void calculateLRSpeeds(float r, float phi) {

  phi = phi * PI / 180.0;
  
  if ((phi >= 0) && (phi < PI / 2.0)) //1st quadrant
  {
      referenceSpeedLeft = r;
      referenceSpeedRight = -r * cosf(2 * phi);
  }
  else if ((phi >= PI / 2.0) && (phi < PI)) //2nd quadrant
  {
      referenceSpeedLeft = -r * cosf(2 * phi);
      referenceSpeedRight = r;
  }
  else if ((phi >= PI) && (phi < 3 * PI / 2.0)) //3rd quadrant
  {
      referenceSpeedLeft = -r;
      referenceSpeedRight = r * cosf(2 * phi);
  }
  else if ((phi >= 3 * PI / 2.0) && (phi <= 2 * PI)) //4th quadrant
  {
      referenceSpeedLeft = r * cosf(2 * phi);
      referenceSpeedRight = -r;
  }
}

void processButtons(uint8_t buttons){
  if ((buttons & 0x01) == 0x01){
    referenceAngleL3_deg += angleIncrement;
  }
  if ((buttons & 0x04) == 0x04){
    referenceAngleL3_deg -= angleIncrement;
  }
  if ((buttons & 0x02) == 0x02){
    referenceAngleR3_deg += angleIncrement;
  }
  if ((buttons & 0x08) == 0x08){
    referenceAngleR3_deg -= angleIncrement;
  }
  
  if ((buttons & 0x10) == 0x10){
    autonomousActive = 1;
  }
  else {
    autonomousActive = 0;
  }

  //else{
  //  //referenceAngleL3_deg = wheelL3Angle_deg;
  //}
}
/* USER CODE END 4 */

/* USER CODE BEGIN Header_StartDefaultTask */
/**
  * @brief  Function implementing the defaultTask thread.
  * @param  argument: Not used 
  * @retval None
  */
/* USER CODE END Header_StartDefaultTask */
void StartDefaultTask(void const * argument)
{

  /* USER CODE BEGIN 5 */
  /* Infinite loop */
  for(;;)
  {
    osDelay(1);
  }
  /* USER CODE END 5 */ 
}
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

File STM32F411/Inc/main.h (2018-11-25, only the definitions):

#define BUZZER_PWM_Pin GPIO_PIN_6
#define BUZZER_PWM_GPIO_Port GPIOE
#define LEFT2_FW_Pin GPIO_PIN_13
#define LEFT2_FW_GPIO_Port GPIOC
#define LEFT2_RW_Pin GPIO_PIN_14
#define LEFT2_RW_GPIO_Port GPIOC
#define PH0_OSC_IN_Pin GPIO_PIN_0
#define PH0_OSC_IN_GPIO_Port GPIOH
#define PH1_OSC_OUT_Pin GPIO_PIN_1
#define PH1_OSC_OUT_GPIO_Port GPIOH
#define SEN1_Pin GPIO_PIN_0
#define SEN1_GPIO_Port GPIOC
#define SEN2_Pin GPIO_PIN_1
#define SEN2_GPIO_Port GPIOC
#define SEN3_Pin GPIO_PIN_2
#define SEN3_GPIO_Port GPIOC
#define SEN4_Pin GPIO_PIN_3
#define SEN4_GPIO_Port GPIOC
#define SERVO5_Pin GPIO_PIN_0
#define SERVO5_GPIO_Port GPIOA
#define SERVO6_Pin GPIO_PIN_1
#define SERVO6_GPIO_Port GPIOA
#define BAT1_Pin GPIO_PIN_2
#define BAT1_GPIO_Port GPIOA
#define BAT2_Pin GPIO_PIN_3
#define BAT2_GPIO_Port GPIOA
#define SEN1_OUT_Pin GPIO_PIN_4
#define SEN1_OUT_GPIO_Port GPIOA
#define SEN2_OUT_Pin GPIO_PIN_5
#define SEN2_OUT_GPIO_Port GPIOA
#define RIGHT1_FW_Pin GPIO_PIN_6
#define RIGHT1_FW_GPIO_Port GPIOA
#define RIGHT1_RW_Pin GPIO_PIN_7
#define RIGHT1_RW_GPIO_Port GPIOA
#define SEN3_OUT_Pin GPIO_PIN_4
#define SEN3_OUT_GPIO_Port GPIOC
#define SEN4_OUT_Pin GPIO_PIN_5
#define SEN4_OUT_GPIO_Port GPIOC
#define SERVO3_Pin GPIO_PIN_0
#define SERVO3_GPIO_Port GPIOB
#define SERVO4_Pin GPIO_PIN_1
#define SERVO4_GPIO_Port GPIOB
#define RIGHT1_ENC_B_Pin GPIO_PIN_7
#define RIGHT1_ENC_B_GPIO_Port GPIOE
#define RIGHT2_ENC_B_Pin GPIO_PIN_8
#define RIGHT2_ENC_B_GPIO_Port GPIOE
#define LEFT1_PWM_Pin GPIO_PIN_9
#define LEFT1_PWM_GPIO_Port GPIOE
#define LEFT2_PWM_Pin GPIO_PIN_11
#define LEFT2_PWM_GPIO_Port GPIOE
#define LEFT3_PWM_Pin GPIO_PIN_13
#define LEFT3_PWM_GPIO_Port GPIOE
#define RIGHT1_PWM_Pin GPIO_PIN_14
#define RIGHT1_PWM_GPIO_Port GPIOE
#define RIGHT3_PWM_Pin GPIO_PIN_10
#define RIGHT3_PWM_GPIO_Port GPIOB
#define LEFT1_ENC_B_Pin GPIO_PIN_12
#define LEFT1_ENC_B_GPIO_Port GPIOB
#define LEFT2_ENC_B_Pin GPIO_PIN_13
#define LEFT2_ENC_B_GPIO_Port GPIOB
#define LEFT3_ENC_B_Pin GPIO_PIN_14
#define LEFT3_ENC_B_GPIO_Port GPIOB
#define LEFT1_FW_Pin GPIO_PIN_15
#define LEFT1_FW_GPIO_Port GPIOB
#define SEN3_EXTI_Pin GPIO_PIN_8
#define SEN3_EXTI_GPIO_Port GPIOD
#define SEN3_EXTI_EXTI_IRQn EXTI9_5_IRQn
#define SEN4_EXTI_Pin GPIO_PIN_9
#define SEN4_EXTI_GPIO_Port GPIOD
#define SEN4_EXTI_EXTI_IRQn EXTI9_5_IRQn
#define RIGHT3_ENC_B_Pin GPIO_PIN_10
#define RIGHT3_ENC_B_GPIO_Port GPIOD
#define LEFT1_RW_Pin GPIO_PIN_11
#define LEFT1_RW_GPIO_Port GPIOD
#define RIGHT3_FW_Pin GPIO_PIN_12
#define RIGHT3_FW_GPIO_Port GPIOD
#define RIGHT3_RW_Pin GPIO_PIN_13
#define RIGHT3_RW_GPIO_Port GPIOD
#define LD5_Pin GPIO_PIN_14
#define LD5_GPIO_Port GPIOD
#define LD6_Pin GPIO_PIN_15
#define LD6_GPIO_Port GPIOD
#define HM_10_Pin GPIO_PIN_6
#define HM_10_GPIO_Port GPIOC
#define HM_10C7_Pin GPIO_PIN_7
#define HM_10C7_GPIO_Port GPIOC
#define SENSOR_SDA_Pin GPIO_PIN_9
#define SENSOR_SDA_GPIO_Port GPIOC
#define SENSOR_SCL_Pin GPIO_PIN_8
#define SENSOR_SCL_GPIO_Port GPIOA
#define RIGHT2_FW_Pin GPIO_PIN_9
#define RIGHT2_FW_GPIO_Port GPIOA
#define RIGHT2_RW_Pin GPIO_PIN_10
#define RIGHT2_RW_GPIO_Port GPIOA
#define SWDIO_Pin GPIO_PIN_13
#define SWDIO_GPIO_Port GPIOA
#define SWCLK_Pin GPIO_PIN_14
#define SWCLK_GPIO_Port GPIOA
#define RIGHT2_PWM_Pin GPIO_PIN_15
#define RIGHT2_PWM_GPIO_Port GPIOA
#define LEFT3_FW_Pin GPIO_PIN_10
#define LEFT3_FW_GPIO_Port GPIOC
#define LEFT3_RW_Pin GPIO_PIN_11
#define LEFT3_RW_GPIO_Port GPIOC
#define LEFT1_EXTI0_Pin GPIO_PIN_0
#define LEFT1_EXTI0_GPIO_Port GPIOD
#define LEFT1_EXTI0_EXTI_IRQn EXTI0_IRQn
#define LEFT2_EXTI1_Pin GPIO_PIN_1
#define LEFT2_EXTI1_GPIO_Port GPIOD
#define LEFT2_EXTI1_EXTI_IRQn EXTI1_IRQn
#define LEFT3_EXTI2_Pin GPIO_PIN_2
#define LEFT3_EXTI2_GPIO_Port GPIOD
#define LEFT3_EXTI2_EXTI_IRQn EXTI2_IRQn
#define RIGHT1_EXTI3_Pin GPIO_PIN_3
#define RIGHT1_EXTI3_GPIO_Port GPIOD
#define RIGHT1_EXTI3_EXTI_IRQn EXTI3_IRQn
#define RIGHT2_EXTI4_Pin GPIO_PIN_4
#define RIGHT2_EXTI4_GPIO_Port GPIOD
#define RIGHT2_EXTI4_EXTI_IRQn EXTI4_IRQn
#define RIGHT3_EXTI5_Pin GPIO_PIN_5
#define RIGHT3_EXTI5_GPIO_Port GPIOD
#define RIGHT3_EXTI5_EXTI_IRQn EXTI9_5_IRQn
#define SEN1_EXTI_Pin GPIO_PIN_6
#define SEN1_EXTI_GPIO_Port GPIOD
#define SEN1_EXTI_EXTI_IRQn EXTI9_5_IRQn
#define SEN2_EXTI_Pin GPIO_PIN_7
#define SEN2_EXTI_GPIO_Port GPIOD
#define SEN2_EXTI_EXTI_IRQn EXTI9_5_IRQn
#define SWO_Pin GPIO_PIN_3
#define SWO_GPIO_Port GPIOB
#define SERVO1_Pin GPIO_PIN_4
#define SERVO1_GPIO_Port GPIOB
#define SERVO2_Pin GPIO_PIN_5
#define SERVO2_GPIO_Port GPIOB
#define Audio_SCL_Pin GPIO_PIN_6
#define Audio_SCL_GPIO_Port GPIOB
#define WS2812_PWM_Pin GPIO_PIN_7
#define WS2812_PWM_GPIO_Port GPIOB
#define WS2812_Pin GPIO_PIN_8
#define WS2812_GPIO_Port GPIOB

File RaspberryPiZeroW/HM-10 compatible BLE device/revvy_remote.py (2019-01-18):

from gi.repository import GLib
import time

import serial

# Bluezero modules
from bluezero import peripheral

# constants
HM_10_UART_SERIVCE = '0000FFE0-0000-1000-8000-00805F9B34FB'
HM_10_UART_CHARACTERISTIC = '0000FFE1-0000-1000-8000-00805F9B34FB'

# connected = False

ser = serial.Serial(
  port='/dev/ttyS0',
  baudrate = 115200,
  parity=serial.PARITY_NONE,
  stopbits=serial.STOPBITS_ONE,
  bytesize=serial.EIGHTBITS,
  timeout=1
)

def sendCommand(command):
    global ser
    # ser.write(b"kaka\n")
    ser.write(command)
    # time.sleep(1)

bleTransferBytes = bytearray([0xFF,0x01,0x02,0x03,0xFF])
newMessage = False
    
class UartService:
    def __init__(self):
        self.app = peripheral.Application()
        self.ble_uart = peripheral.Service(HM_10_UART_SERIVCE,
                                           True)
        self.rxtx_uart = peripheral.Characteristic(HM_10_UART_CHARACTERISTIC,
                                                 ['write',
                                                  'write-without-response',
                                                  'notify'],
                                                 self.ble_uart)

        self.rxtx_uart.add_write_event(self.uart_print)
        self.rxtx_uart.add_notify_event(print)
        self.rxtx_uart.StartNotify()
        self.ble_uart.add_characteristic(self.rxtx_uart)
        self.app.add_service(self.ble_uart)

        self.other_service = peripheral.Service('0000180A-0000-1000-8000-00805F9B34FB', True)
        self.app.add_service(self.other_service)

    @staticmethod
    def _to_bytes(word):
        return [ord(x) for x in word]

    def uart_print(self, value):
        global bleTransferBytes
        global newMessage
        # print(value)
        # print("%d;%d;%d;%d;%d" % (int(value[0]),int(value[1]),int(value[2]),int(value[3]),int(value[4])))
        bleTransferBytes[0] = value[0]
        bleTransferBytes[1] = value[1]
        bleTransferBytes[2] = value[2]
        bleTransferBytes[3] = value[3]
        bleTransferBytes[4] = value[4]

        newMessage = True
        # if (connected == False):
            # print('connected')
            # connected = True

    def start(self):
        self.app.start()

    def stop(self):
        self.app.stop()


def sender(dev_loop):
    global bleTransferBytes
    global newMessage
    # time.sleep(1)
    # if (connected):
        # dev_loop.rxtx_uart.send_notify_event('buzi')
    # print("Message sent")
    # return True
    if (newMessage == True):
        # print(bleTransferBytes)
        sendCommand(bleTransferBytes)
        newMessage = False
        
    # time.sleep(1)
    # sendCommand(bleTransferBytes)
    return True



if __name__ == '__main__':
    # dev = InputDevice('/dev/input/event0')
    ser.close()
    ser.open()
    ser.isOpen()
    
    # while (1):
        # sendCommand("")
        # time.sleep(1)
    
    uart = UartService()
    uart.app.dongle.alias = 'Revvy_RPi'
    # uart.app.dongle.tx_power = 10
    # uart.app.dongle.icon = "folder-new"
    # print(uart.app.dongle.name)
    # print("***")
    GLib.idle_add(sender, uart)
    uart.start()

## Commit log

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2018-11-04 MCU pinout table was added Cleanup of unused source files Cleanup of naming conventions in CubeMX project 4x ultrasonic distance sensors are working with 10us resolution 6x encoder signals are proces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
    [MCU_pinout.csv, MCU_pinout.xlsx]
2018-11-04 Buzzer changed from TIM9_CH1 to CH2, it's working now Pinout updated
    [MCU_pinout.csv, MCU_pinout.xlsx]
2018-11-14 2018-11-14: - Schematic is now uploaded - WS2812 was unreliable with TIM+DMA, it might be a HW bug in ST's HW - WS2812 is now driven on SPI5+DMA, pin moved to PB8 from PB7 - WS2812 library contains n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
    ToDo:
    - WS2812 library cleanup is needed!
    - Compass is not calibrated yet
    - 6 PID controller
    - USB Host?
    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
    [MCU_pinout.xlsx]
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2018-11-16 Cleanup WS2812 driver source
    Extract shift/rotate functions to avoid duplication, implement 3bit/bit encoding for SPI, allow disabling of timer or spi
    [WS2812_Lib.c]
2018-11-16 Update WS2812 driver header
    Add some configuration macros: reset bit count and output peripherial enable
    [WS2812_Lib.h]
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2018-11-17 2018-11-17: - Structural parts added
    [2x10.stp, 2x20.stp, 2x30.stp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]
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2018-11-17 Fix bit pattern
    Last bit pattern should be 0x06 = 0b00000110
    [WS2812_Lib.c]
2018-11-17 Fix low bits
    Low bits were incorrectly generated, use a precomputed LUT for them as well - in this case, no special case is necessary because we set only one bit per LED-bit.
    [WS2812_Lib.c]
2018-11-20 SolidWorks model of TT motor with encoder
    [Encoder.sldprt, FIT0450.SLDASM, Gearbox.sldprt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]
2018-11-22 BOM added
    [Bill-of-Materials-Revvy-Demo.xls]
2018-11-22 Motor converted to inventor
    [Encoder.ipt, FIT0450.STEP, FIT0450.iam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]
2018-11-24 2018-11-24: - Toolchain updated to STM32CubeMX 5.0.0 with STM32CubeF4 Firmware Package V1.22.0 / 02-November-2018 - Bluetooth tested - Battery voltage measurement factor corrected
    [RevvyDemo.ioc, main.c, main.h]
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2018-11-25 Motor rotor step, stl added
    [Motor rotor.stl, Motor rotor.stp]
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2018-11-25 Motor rotor fixed (ipt, stl, step)
    [Axle 2.ipt, Motor assembly.iam, Motor rotor.ipt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]
2018-11-28 Updated brain case parts and bugfixes
    [BottomCase^_BRAIN.sldprt, UpperCase.STL, UpperCase^_BRAIN.sldprt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]
2018-11-28 Brain case bugfix
    [_BRAIN_V2.SLDASM, bottom_part_v2.STL, bottom_part_v2.sldprt]
2018-12-04 Motor cover before resizing
    [Motor assembly.iam, Motor cover lower.ipt, Motor cover upper.ipt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]
2018-12-04 Motor cover first version
    [Axle 2.stl, Motor assembly.iam, Motor cover lower.ipt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]
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2018-12-07 Add new motor rotor, ultrasonic enclosure and wheel models
    [Motor rotor_mod.SLDPRT, Motor rotor_mod.STL, Part2^SensorCase.STL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]
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2019-01-11 Raspberry Pi HM-10 compatible BLE device Structural parts update Bugfixes
    [2x4.stl, 2x4.stp, Axle 2.sldprt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]
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2019-01-25 Gear (4,6) inventor parts added
    [gear20.ipt, gear40.iam, gear40.ipt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]
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2019-01-25 Adjusted axle and gear square hole diameter, new gearprofiles in inventor gear parts
    [Axle 2.ipt, Axle 2.stl, Axle 5s.ipt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]
2019-01-28 Gear rack added, Small gear collar increased
    [2x30.ipt, 2x4.ipt, Base_part.ipt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]
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2019-01-30 Bent beams
    [Bent Beam 5-T.ipt, Bent beam 5-120.ipt, Bent beam 5-120.stl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]
2019-01-31 Curved beams fixed with 66 mm inner diameter Straight beams SXx1 and SXx2 added
    [20_60.dxf, 20_new.dxf, 2x10.stp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]
2019-01-31 Straight beams redesigned: modular buildup. SXx4, SXx2, SXx1 ok
    [Base_part.ipt, Plastic part checklist.xlsx, S12x1.iam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]
2019-02-01 SXx4, V, L, T shaped beams added
    [2x10.stp, 2x20.stp, 2x30.ipt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]
2019-02-01 Changed inner wall thickness (SXx2, SXx4) and end part fillet removal
    [S12x2.iam, S12x2.stl, S16x2.iam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]
2019-02-04 Curved beam CB4H added
    [CB4H-40D-30L.ipt, CB4H-40D-35,5L.ipt, CB4H-40D-35L.ipt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]
2019-02-04 Axle, gear hole/diameter fillet/size modified
    [Axle 2.ipt, Axle 2.stl, Axle 5s.ipt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]
2019-02-06 Some axles, round beams, connector pins added
    [AXp12s.ipt, AXp12s.stl, AXp2+c.ipt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]
2019-02-06 Connector triangles, boxes added
    [AXp12s.ipt, AXp2+c.ipt, AXp2+s.ipt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]
2019-02-07 CC2x2 fixed, wedges, Axle beams added
    [AXb1.iam, AXb1.stl, AXb3.iam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]
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2019-02-12 Gear redesign, Volume computation, STEP export for RFQ
    [A120.iam, A120.ipt, A120.stl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]
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2019-02-12 Colored parts, v214 STEP file generated
    [2x10.stp, 2x20.stp, 2x30.stp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]
2019-02-12 Pin related parts updated, Steps generated
    [AXp12s.ipt, AXp12s.stl, AXp12s.stp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]
2019-02-12 Overall update of 3D models
    [0204 - Capacitor Brown.sldprt, 0204 - Capacitor.sldprt, 0204- Resistor.sldprt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]
2019-02-13 S3x4, S4x3 added, Gears fixed to be the holes in line
    [G20.iam, G20.ipt, G20.stl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]
2019-02-14 S4x3 added to RFQ folder
    [S4x3.stp]
2019-02-14 update with final RFQ list
    [Plastic part checklist.xlsx]
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2019-02-14 Inventor imports for demo buildup
    [0204 - Capacitor Brown.ipt, 0204 - Capacitor.ipt, 0204- Resistor.ipt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]
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2019-02-14 Part test assembly v1
    [EL8.ipt, EL8_multipart.ipt, MOcA_1.ipt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]
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2019-02-18 EL8 plus inner walls added
    [EL8.stl, EL8.stp, EL8_multipart.ipt]
2019-02-18 EL8 plus inner walls added (forgotten save)
    [EL8.ipt]
2019-02-18 Brain simplified, Inventor imports
    [0204 - Capacitor Brown.ipt, 0204 - Capacitor.ipt, 0204- Resistor.ipt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]
2019-02-21 Battery holder redesign with battery holder pack
    [6AA.iam, BAcA.ipt, BAcA.stl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]
2019-02-22 Battery holder redesign, and split for easier 3D print
    [BAcA.iam, BAcA.ipt, BAcA_3.ipt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]
2019-02-25 Ultrasonic Assembly design added
    [0603 Capacitor.ipt, 0603 Resistor.ipt, A120.ipt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]
2019-02-28 SLS print collection Rev 1
    [AXp12s.stl, AXp12s.stp, AXp2p test assembly.iam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]
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2019-03-04 CP1x1 test assembly step regenerated
    [CP1x1 test assembly.stp]
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2019-03-08 Brain softeq cleanup - shrinkwrap
    [0204 - Capacitor Brown.ipt, 0204 - Capacitor.ipt, 0204- Resistor.ipt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]
2019-03-11 Round beam grooves added
    [RB1+.iam, RB1.iam, RB1.ipt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]
2019-03-13 3pi caster wheel added
    [mini_3pi_caster_ball.ipt, mini_3pi_caster_body.ipt, mini_3pi_caster_wheel.iam]
2019-03-13 Small modification is STEP files
    [BRcA_3.STEP, MOcA_1.STEP, MOcA_2.STEP]
2019-03-14 Alpha kit SLS print collection
    [AXp2p.iam, AXp2p.stl, AXp2p.stp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]
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2019-03-18 Save before test assemblies
    [BAcA_assembly.iam, Battery_holder_WZY-148-1_with_cable.Harness1.iam, Battery_holder_WZY-148-1_with_cable.iam]
2019-03-20 Brain wall thickness hotfix
    [BRcA.ipt, BRcA_1.ipt, BRcA_1.stp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]
2019-03-20 Brain hotfix copied to quotation2
    [BRcA_1.stp, BRcA_2.stp]
2019-03-21 Test assemblies ver 1 - for Jared Fusion 360 test
    [BAcA_1.ipt, BAcA_assembly.iam, BUcA_1.ipt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]
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2019-03-27 Color updates in assembly
    [motor.SLDASM]
2019-03-27 Caster wheel adapters added
    [Caster_wheel_inner_plug_1.ipt, Caster_wheel_inner_plug_1.stl, Caster_wheel_inner_plug_1.stp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]
2019-03-28 Motor pack RFQ updates
    [MOhA.sldprt, motor.SLDDRW, motor.STEP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]
2019-03-28 Caster wheel inner plugs
    [Caster_wheel_inner_plug_1.ipt, Caster_wheel_inner_plug_1_01.ipt, Caster_wheel_inner_plug_1_01.stl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]
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2019-04-01 Just saves, and minor changes
    [Alpha Kit BoM.xlsx, BAcA_2.ipt, BAcA_assembly.iam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]
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2019-04-10 Failure report
    [A135.stp, A90L.stp, A90T.stp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]
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2019-04-10 Fixed alpha kit file - could be opened in Inventor 2019
    [PCBA_estimation_20190215.iam]
2019-04-11 Kickstarter video designs added
    [0204 - Capacitor Brown.ipt, 0204 - Capacitor.ipt, 0204- Resistor.ipt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]
2019-04-12 Brain for kickstarter video
    [Brain_for_kickstarter_video.ipn]
2019-04-16 Very basic part replacements in kickstarter video
    [BRcA.ipt, Brain_demo_PCB.ipt, Brain_for_kickstarter_video_demo.iam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]
2019-04-25 Ultrasonic sensor STEP file uploaded
    [UltrasonicSensor2_ver2.STEP]
2019-04-25 Kickstarter videos full assembly
    [HC-SR04.ipt, MOcA_1.ipt, MOcA_2.ipt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]
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2019-05-05 Backup before migrating Inventor 2020
    [Full kit assembly.ipn, bumper.iam, bumper_for_pcb_design.stp]
2019-12-23 Update files to match local copy
    update app logic to the latest version
    remove a huge brain 3D model file
    [0204 - Capacitor Brown.sldprt, 0204 - Capacitor.sldprt, 0204- Resistor.sldprt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]
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

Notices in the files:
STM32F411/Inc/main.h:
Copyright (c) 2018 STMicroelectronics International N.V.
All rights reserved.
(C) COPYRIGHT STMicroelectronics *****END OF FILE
